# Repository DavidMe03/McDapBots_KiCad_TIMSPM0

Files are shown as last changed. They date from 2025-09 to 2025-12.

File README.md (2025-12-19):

# McDap Bots Pedagogical Robot

This project was created as a capstone project for the University of Virginia Department of Electrical and Computer Engineering. Our goal was to create a small robot which could be programmed by students, for use as a teaching aide in an embedded systems course. This repository contains the hardware files specific to the robot's main board.

**Authors**
- Colby Wise
- Pratik Pandit
- Austen Yun 
- David Merino
- Marc Rosenthal

**Advisors**: Todd DeLong and Adam Barnes 

**Features at a glance**
- 2 motors (PWM controlled), OLED screen (I2C), reflectance sensor (I2C), bump switches (GPIO), Bluetooth (UART), and infrared sensors (ADC)
- battery charging port and battery voltage display (press button to enable)
- support for TI and STM microcontrollers

## What is contained here

**Project Symbols/Footprints**

Symbols that are specific to this project such as the robot chassis. 

**Schematic File**

KiCad schematic file that shows the electrical connections of each component of the robot. 

**Layout File**

KiCad layout file that shows how the components are placed and routed on the PCB. 

**Bill of Materials Files**

BOM.xlsx contains a list of all the parts needed for the PCB.

Digikey_Parts_List.xlsx can be uploaded to Digikey to select the parts needed for one copy of this board.

## How to use this repository
1. Copy the repository locally to your computer
2. Using KiCad 8.0 (or higher version) open the file `MotorBoardv3_2.kicad_pro`
3. Generate necessary gerber files and order components
4. Follow the provided construction guide to build the robot

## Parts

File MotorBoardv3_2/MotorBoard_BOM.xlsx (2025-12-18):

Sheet: MotorBoardv3_2
Main PCB Parts
Id | Designator | Footprint | Quantity | Designation | Supplier | Link | Notes
1 | LED1 | APT1608CGCK | 1 | 3.3V | Digikey | APTD1608LSECK/J3-PF Kingbright | Optoelectronics | DigiKey (https://www.digikey.com/en/products/detail/kingbright/aptd1608lseck-j3-pf/5177446) | Red LED to indicate robot on/off
2 | CHARGE | APT1608CGCK | 1 | 3.3V | Digikey | APTD1608LZGCK Kingbright | Optoelectronics | DigiKey (https://www.digikey.com/en/products/detail/kingbright/APTD1608LZGCK/5177450) | Green LED to indicate battery charging
3 | R1,R2,R4,R13,R14 | R_0603_1608Metric | 5 | 4.7k | Digikey | RC0603FR-104K7L YAGEO | Resistors | DigiKey (https://www.digikey.com/en/products/detail/yageo/RC0603FR-104K7L/13694213) | Resistors
4 | R3,R12 | R_0603_1608Metric | 2 | 1.5k | Digikey | RC0603FR-071K5L YAGEO | Resistors | DigiKey (https://www.digikey.com/en/products/detail/yageo/RC0603FR-071K5L/726864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) | Resistors
5 | R5,R6 | R_1206_3216Metric | 2 | 0.1 | Digikey | RCWL1206R100JMEA Vishay Dale | Resistors | DigiKey (https://www.digikey.com/en/products/detail/vishay-dale/rcwl1206r100jmea/5777316) | Resistors
6 | R7 | R_0603_1608Metric | 1 | 750 | Digikey | RC0603JR-07750RL YAGEO | Resistors | DigiKey (https://www.digikey.com/en/products/detail/yageo/rc0603jr-07750rl/726825) | Resistor
7 | R8 | R_0603_1608Metric | 1 | 1.4k | Digikey | RC0603FR-071K4L YAGEO | Resistors | DigiKey (https://www.digikey.com/en/products/detail/yageo/RC0603FR-071K4L/726861) | Resistor
8 | R9 | R_0603_1608Metric | 1 | 68K | Digikey | RT0603FRE0768KL YAGEO | Resistors | DigiKey (https://www.digikey.com/en/products/detail/yageo/rt0603fre0768kl/1075464) | Resistor
9 | R10 | R_0603_1608Metric | 1 | 22K | Digikey | RC0603JR-0722KL YAGEO | Resistors | DigiKey (https://www.digikey.com/en/products/detail/yageo/rc0603jr-0722kl/726744) | Resistor
10 | R11 | R_0603_1608Metric | 1 | 150 | Digikey | RMCF0603FT150R Stackpole Electronics Inc | Resistors | DigiKey (https://www.digikey.com/en/products/detail/stackpole-electronics-inc/RMCF0603FT150R/1761314) | Resistor
11 | R_Sense1 | R_0603_1608Metric | 1 | 590m | Digikey | RLT0816-3-R590-FNH Delta Electronics/Cyntec | Resistors | DigiKey (https://www.digikey.com/en/products/detail/delta-electronics-cyntec/rlt0816-3-r590-fnh/9762157) | Resistor
12 | C1,C2,C3,C4,C5,C6,C7,C8 | CAPPM3528X210N | 8 | 10uF | Digikey | TAJB106K020RNJ KYOCERA AVX | Capacitors | DigiKey (https://www.digikey.com/en/products/detail/kyocera-avx/TAJB106K020RNJ/563780) | Capacitors (Polar)
13 | C9 | C_0603_1608Metric | 1 | 0.1uF | Digikey | CC0603KRX7R7BB104 YAGEO | Capacitors | DigiKey (https://www.digikey.com/en/products/detail/yageo/CC0603KRX7R7BB104/302822) | Capacitor
14 | C11,C15 | C_0603_1608Metric | 2 | 10uF | Digikey | TCM0J106M8R KYOCERA AVX | Capacitors | DigiKey (https://www.digikey.com/en/products/detail/kyocera-avx/TCM0J106M8R/1209640) | Capacitors (Polar)
15 | C12 | C_0603_1608Metric | 1 | 1uF | Digikey | CL10B105KP8NNNC Samsung Electro-Mechanics | Capacitors | DigiKey (https://www.digikey.com/en/products/detail/samsung-electro-mechanics/CL10B105KP8NNNC/3887604) | Capacitor
16 | C13,C14 | C_0603_1608Metric | 2 | 0.01uF | Digikey | C0603C103K5RACTU KEMET | Capacitors | DigiKey (https://www.digikey.com/en/products/detail/kemet/C0603C103K5RACTU/411090) | Capacitors
17 | D1 | D_DO-41_SOD81_P10.16mm_Horizontal | 1 | 1N4001 | Digikey | 1N4001-TP MCC (Micro Commercial Components) | Discrete Semiconductor Products | DigiKey (https://www.digikey.com/en/products/detail/mcc-micro-commercial-components/1N4001-TP/773688) | Rectifier Diode
18 | Q1 | TO-220-3_Vertical | 1 | TIP42A | Digikey | TIP42A STMicroelectronics | Discrete Semiconductor Products | DigiKey (https://www.digikey.com/en/products/detail/stmicroelectronics/TIP42A/603577) | PNP Transistor
19 | U1 | SOP65P640X120-17N | 1 | DRV8847PWPR | Digikey | DRV8847PWR Texas Instruments | Integrated Circuits (ICs) | DigiKey (https://www.digikey.com/en/products/detail/texas-instruments/DRV8847PWR/9954205) | Motor Driver IC
20 | U2 | SOT230P700X180-4N | 1 | LM2937IMP-5.0_NOPB | Digikey | LM2937IMP-5.0/NOPB Texas Instruments | Integrated Circuits (ICs) | DigiKey (https://www.digikey.com/en/products/detail/texas-instruments/LM2937IMP-5-0-NOPB/270743) | 5V Linear Regulator IC
21 | U3 | SOT230P700X180-4N | 1 | LM2937IMP-3.3_NOPB | Digikey | LM2937IMP-3.3 Texas Instruments | Integrated Circuits (ICs) | DigiKey (https://www.digikey.com/en/products/detail/texas-instruments/LM2937IMP-3-3/3701483) | 3.3V Linear Regulator IC
22 | U4 | SSD1306 | 1 | SSD1306 | Amazon | Amazon.com: Hosyond 5 Pcs 0.96 Inch OLED I2C IIC Display Module 12864 128x64 Pixel SSD1306 Mini Self-Luminous OLED Screen Board Compatible with Arduino Raspberry Pi (White) : Electronics (https://www.amazon.com/Hosyond-Display-Self-Luminous-Compatible-Raspberry/dp/B09T6SJBV5) | OLED Display Board, can be soldered directly onto PCB
23 | U7 | SOIC-16_3.9x9.9mm_P1.27mm | 1 | MAX712CSE | Digikey | MAX712CSE+T Analog Devices Inc./Maxim Integrated | Integrated Circuits (ICs) | DigiKey (https://www.digikey.com/en/products/detail/analog-devices-inc-maxim-integrated/MAX712CSE-T/1521014) | Charge Controller IC
24 | DS1 | PRT-14313 | 1 | ~ | Digikey | 14313 SparkFun Electronics | Industrial Automation and Controls | DigiKey (https://www.digikey.com/en/products/detail/sparkfun-electronics/14313/7564745) | Voltmeter LED Display
25 | S1 | SW_TS02-66-50-BK-160-LCR-D | 1 | TS02-66-50-BK-160-LCR-D | Digikey | TS02-66-50-BK-160-LCR-D Same Sky (Formerly CUI Devices) | Switches | DigiKey (https://www.digikey.com/en/products/detail/same-sky-formerly-cui-devices/TS02-66-50-BK-160-LCR-D/15634352) | SPST Tactile Switch for voltmeter
26 | J6 | 500SSP1S2M2QEA | 1 | 500SSP1S2M2QEA | Digikey | 500SSP1S2M2QEA E-Switch | Switches | DigiKey (https://www.digikey.com/en/products/detail/e-switch/500ssp1s2m2qea/1803993) | Robot power on/off slide switch
27 | J9 | TENSILITY_54-00127 | 1 | 54-00127 | Digikey | 54-00127 Tensility International Corp | Connectors, Interconnects | DigiKey (https://www.digikey.com/en/products/detail/tensility-international-corp/54-00127/9685436) | DC barrel jack port
28 | J2_J4,J3_J1 | LaunchPad | 2 | LaunchPad | Digikey | M20-8761042P Harwin Inc. | Connectors, Interconnects | DigiKey (https://www.digikey.com/en/products/detail/harwin-inc/M20-8761042P/3919957) | 20 position headers for connecting to the TI Launchpad
29 | J11,J12,J13 | SHDR3W50P0X200_1X3_650X240X440P | 3 | GP2Y0A41SK0F | Digikey | M22-7130342 Harwin Inc. | Connectors, Interconnects | DigiKey (https://www.digikey.com/en/products/detail/harwin-inc/M22-7130342/2264331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) | Female header pins for the IR Sensors
30 | J1,J2,J3,J4 | D2F-01L30-D3_5pin | 4 | Bump1,Bump2,Bump3,Bump4 | Digikey | SS-5GL2 Omron Electronics Inc-EMC Div | Switches | DigiKey (https://www.digikey.com/en/products/detail/omron-electronics-inc-emc-div/SS-5GL2/137204) | Bump switches
31 | J5 | RSLK_Chassis | 2 | RSLK2 | Digikey | CES-106-01-G-S Samtec Inc. | Connectors, Interconnects | DigiKey (https://www.digikey.com/en/products/detail/samtec-inc/ces-106-01-g-s/2172853) | Female header pins for the motors
32 | J10,J21 | PinHeader_1x04_P2.54mm_Vertical | 2 | Reflector Support, Reflector I2C | Digikey | PPTC041LFBN-RC Sullins Connector Solutions | Connectors, Interconnects | DigiKey (https://www.digikey.com/en/products/detail/sullins-connector-solutions/PPTC041LFBN-RC/810144) | Female header pins for the reflectance sensor array
33 | J7,J8,J15,J16,J17,J18 | PinHeader_1x02_P2.54mm_Vertical | 6 | XDS_VCC TP10, LP3.3,7.2,LP5.0,ELA,ERA | Digikey | TSW-120-07-L-S Samtec Inc. | Connectors, Interconnects | DigiKey (https://www.digikey.com/en/products/detail/samtec-inc/tsw-120-07-l-s/1101407) | Male header pins for jumpers
34 | TP1,TP2,TP3,TP4 | Testpoint_1x02_P2.54mm | 4 | +5V,+7.2V,GND,+3.3V | Digikey | TSW-120-07-L-S Samtec Inc. | Connectors, Interconnects | DigiKey (https://www.digikey.com/en/products/detail/samtec-inc/tsw-120-07-l-s/1101407) | Male header pins for test points
Additional Parts
Id | Designator | Footprint | Quantity | Designation | Supplier | Link | Notes
1 |  |  | 3 | IR Sensors | Digikey | GP2Y0A21YK0F SHARP/Socle Technology | Sensors, Transducers | DigiKey (https://www.digikey.com/en/products/detail/sharp-socle-technology/GP2Y0A21YK0F/720159) | 10-80cm IR Sensors
2 |  |  | 1 | Romi Chassis Kit | Pololu | Pololu - Romi Chassis Kit - Black (https://www.pololu.com/product/3500) | Robot chassis, wheels, motors, battery contacts
3 |  |  | 1 | Romi Encoder Pair Kit | Pololu | Pololu - Romi Encoder Pair Kit, 12 CPR, 3.5-18V (https://www.pololu.com/product/3542) | Pair of motor encoders
4 |  |  | 1 | TI MSPM0 Launchpad | Texas Instruments | LP-MSPM0G3507 Evaluation board | TI.com (https://www.ti.com/tool/LP-MSPM0G3507) | MSPM0 Launchpad, development board for the TI microcontroller
5 |  |  | 6 | Shunts | Digikey | 382811-8 TE Connectivity AMP Connectors | Connectors, Interconnects | DigiKey (https://www.digikey.com/en/products/detail/te-connectivity-amp-connectors/382811-8/293121) | Shunts for the jumpers
6 |  |  | 1 | Launchpad Power Connector | Digikey | SSQ-102-01-G-S Samtec Inc. | Connectors, Interconnects | DigiKey (https://www.digikey.com/en/products/detail/samtec-inc/SSQ-102-01-G-S/1110617) | 2-pin female header soldered onto the MSPM0 Launchpad

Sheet: BOM
Reflectance Sensor Adapter Board Parts

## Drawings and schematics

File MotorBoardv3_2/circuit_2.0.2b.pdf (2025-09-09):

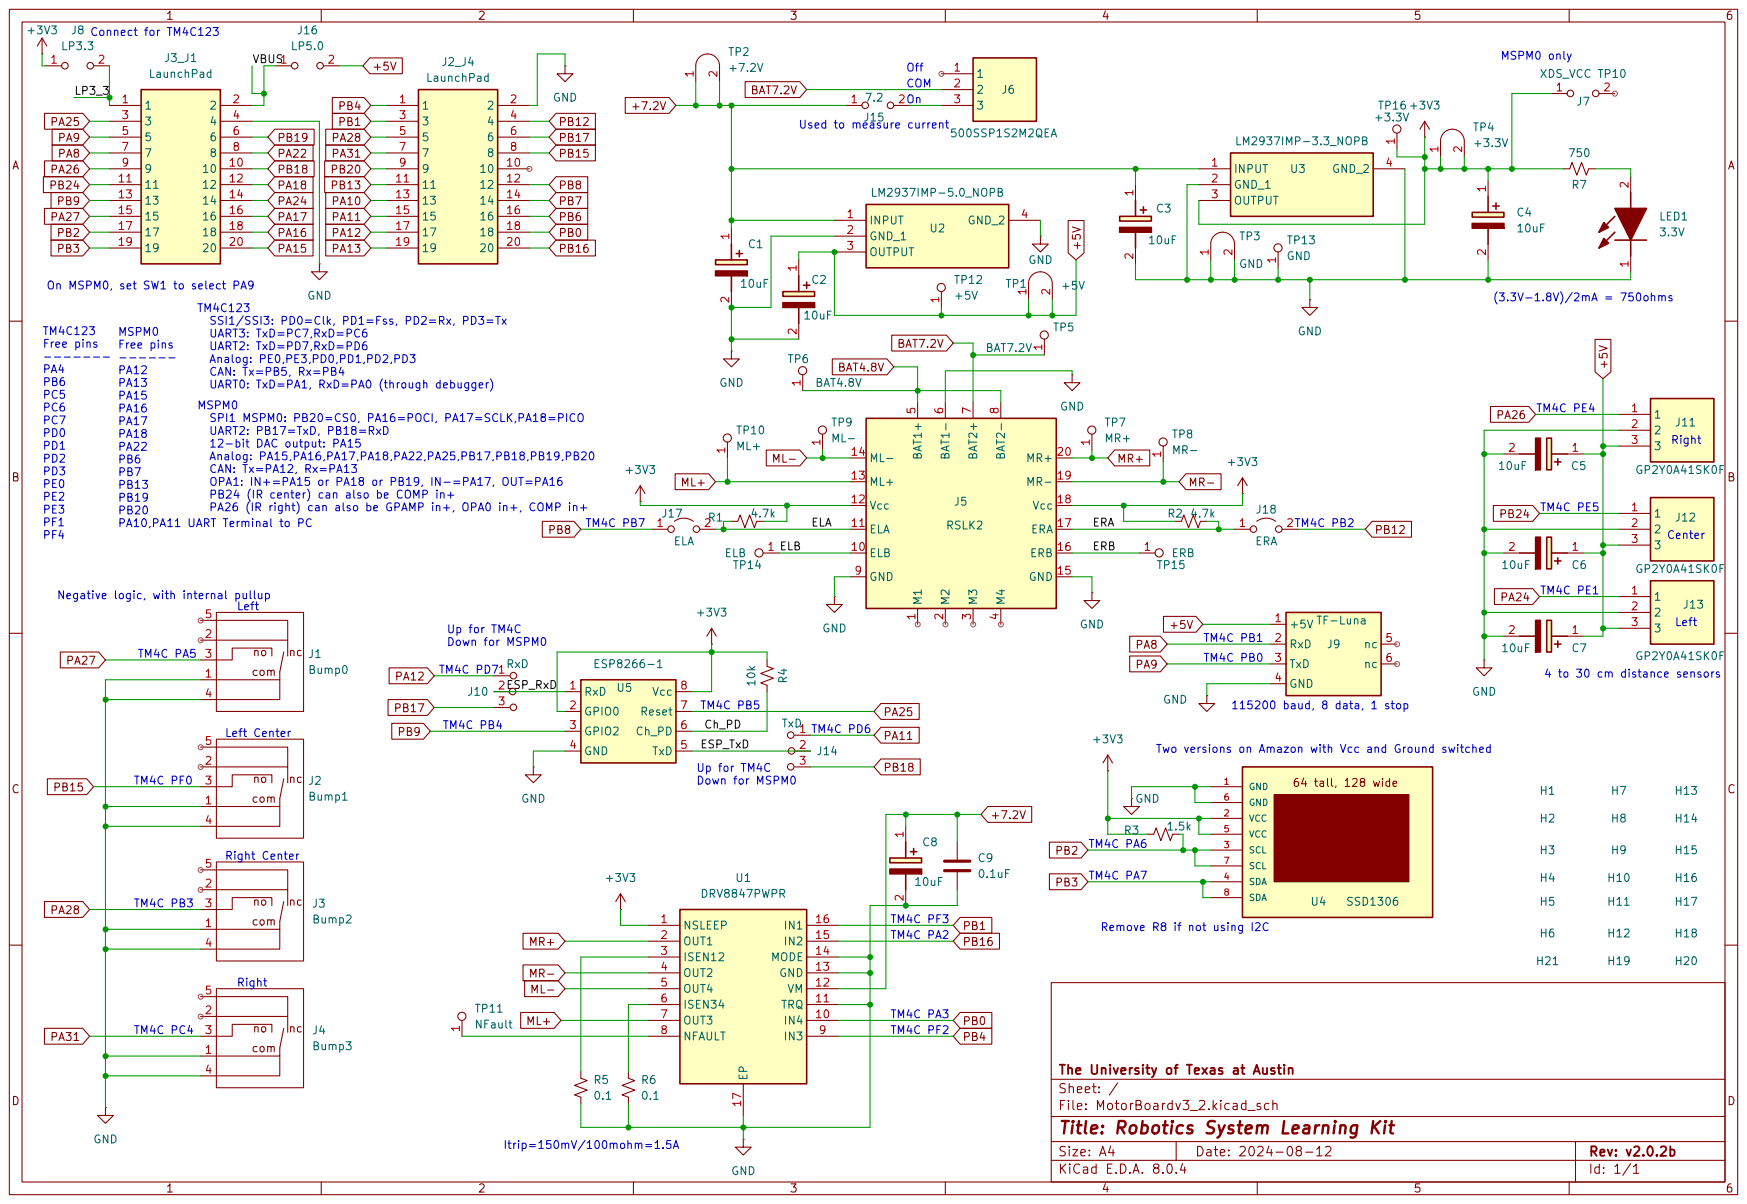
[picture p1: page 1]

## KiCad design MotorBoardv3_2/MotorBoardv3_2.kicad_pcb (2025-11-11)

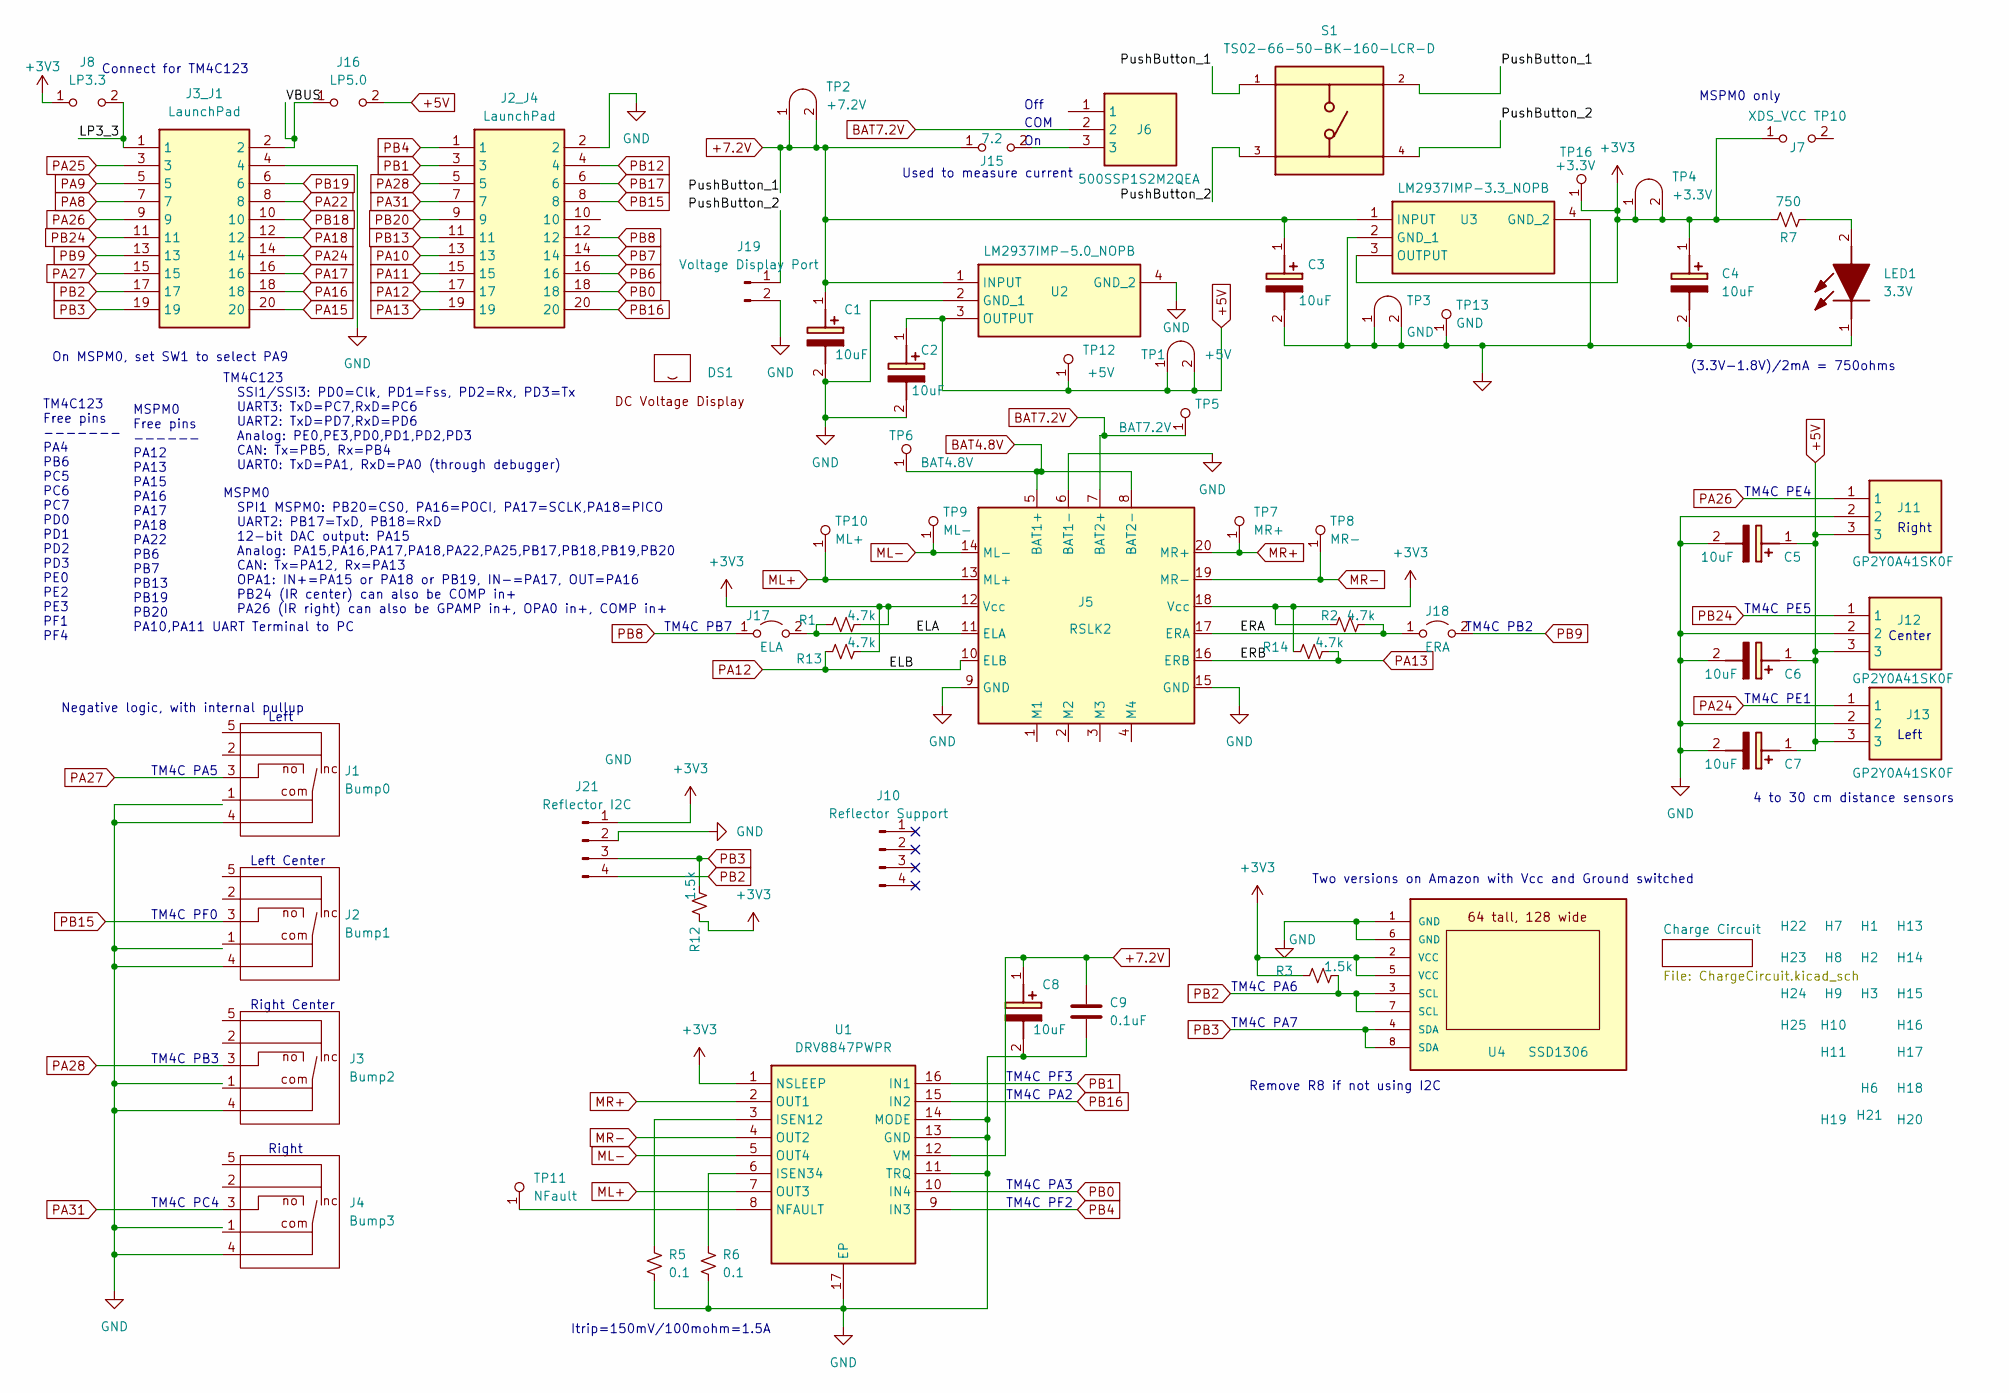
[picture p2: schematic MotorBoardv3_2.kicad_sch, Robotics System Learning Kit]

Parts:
C1, C2, C3, C4, C5, C6, C7, C8: 10uF; CAPPM3528X210N; Mouser Part Number 581-TAJB106K020R
C9: 0.1uF; C_0603_1608Metric; LCSC C5186689
DS1: PRT-14313
H1, H2, H3, H6, H7, H8, H9, H10, H11, H13, H14, H15, H16, H17, H18, H19, H20, H21, H22, H23, H24, H25: MountingHole_4_40
J1: Bump0; D2F-01L30-D3_5pin
J2: Bump1; D2F-01L30-D3_5pin
J2_J4, J3_J1: LaunchPad; Mouser Part Number 855-M20-8761042P
J3: Bump2; D2F-01L30-D3_5pin
J4: Bump3; D2F-01L30-D3_5pin
J5: RSLK2; RSLK_Chassis
J6: 500SSP1S2M2QEA; Mouser Part Number 612-500SSP1S2M2QEA
J7: XDS_VCC TP10; PinHeader_1x02_P2.54mm_Vertical; LCSC C5172712
J8: LP3.3; PinHeader_1x02_P2.54mm_Vertical; LCSC C5172712
J10: Reflector Support; PinHeader_1x04_P2.54mm_Vertical
J11, J12, J13: GP2Y0A41SK0F; SHDR3W50P0X200_1X3_650X240X440P; Mouser Part Number 855-M22-7130342
J15: 7.2; PinHeader_1x02_P2.54mm_Vertical; LCSC C5172712
J16: LP5.0; PinHeader_1x02_P2.54mm_Vertical; LCSC C5172712
J17: ELA; PinHeader_1x02_P2.54mm_Vertical
J18: ERA; PinHeader_1x02_P2.54mm_Vertical
J19: Voltage Display Port; SolderWire-0.15sqmm_1x02_P4mm_D0.5mm_OD1.5mm_Relief
J21: Reflector I2C; PinHeader_1x04_P2.54mm_Vertical
LED1: 3.3V; APT1608CGCK; Mouser Part Number 604-APTD1608LSECKJ3F
R1, R2, R13, R14: 4.7k; R_0603_1608Metric; LCSC C23162
R3, R12: 1.5k; R_0603_1608Metric; LCSC C216914
R5, R6: 0.1; R_1206_3216Metric; LCSC C2889036
R7: 750; R_0603_1608Metric; LCSC C365210
S1: TS02-66-50-BK-160-LCR-D; SW_TS02-66-50-BK-160-LCR-D; PARTREV 1.0
TP1: +5V; Testpoint_1x02_P2.54mm
TP2: +7.2V; Testpoint_1x02_P2.54mm
TP3: GND; Testpoint_1x02_P2.54mm
TP4: +3.3V; Testpoint_1x02_P2.54mm
TP5: BAT7.2V; Testpoint_1x1
TP6: BAT4.8V; Testpoint_1x1
TP7: MR+; Testpoint_1x1
TP8: MR-; Testpoint_1x1
TP9: ML-; Testpoint_1x1
TP10: ML+; Testpoint_1x1
TP11: NFault; Testpoint_1x1
TP12: +5V; Testpoint_1x1
TP13: GND; Testpoint_1x1
TP16: +3.3V; Testpoint_1x1
U1: DRV8847PWPR; SOP65P640X120-17N; Mouser Part Number 595-DRV8847PWPR
U2: LM2937IMP-5.0_NOPB; SOT230P700X180-4N; Mouser Part Number 926-LM2937IMP5.0NOPB
U3: LM2937IMP-3.3_NOPB; SOT230P700X180-4N; Mouser Part Number 926-LM2937IMP3.3NOPB
U4: SSD1306

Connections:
+3V3: C4.1 (+), J5.12 (Vcc), J5.18 (Vcc), J7.1 (A), J8.1 (A), J21.1, R1.2, R2.1, R3.1, R7.2, R12.1, R13.2, R14.1, TP4.1 (A), TP4.2 (B), TP16.1 (A), U1.1 (NSLEEP), U3.3 (OUTPUT), U4.2 (VCC), U4.5 (VCC)
+5V: C2.1 (+), C5.1 (+), C6.1 (+), C7.1 (+), J11.3, J12.3, J13.3, J16.2 (B), TP1.1 (A), TP1.2 (B), TP12.1 (A), U2.3 (OUTPUT)
+7.2V: C1.1 (+), C3.1 (+), C8.1 (+), C9.1, J15.1 (A), S1.1, S1.2, TP2.1 (A), TP2.2 (B), U1.12 (VM), U2.1 (INPUT), U3.1 (INPUT)
/ELA: J5.11 (ELA), J17.2 (B), R1.1
/ERA: J5.17 (ERA), J18.1 (A), R2.2
/LP3_3: J3_J1.1, J8.2 (B)
/PushButton_2: J19.1, S1.3, S1.4
/VBUS: J3_J1.2, J16.1 (A)
BAT4.8V: J5.5 (BAT1+), J5.8 (BAT2-), TP6.1 (A)
BAT7.2V: J5.7 (BAT2+), J6.2, TP5.1 (A); also elsewhere on the board
GND: C1.2 (-), C2.2 (-), C3.2 (-), C4.2 (-), C5.2 (-), C6.2 (-), C7.2 (-), C8.2 (-), C9.2, J1.4 (com), J2.4 (com), J2_J4.2, J3.4 (com), J3_J1.4, J4.4 (com), J5.6 (BAT1-), J5.9 (GND), J5.15 (GND), J11.2, J12.2, J13.2, J19.2, J21.2, LED1.1 (K), R5.2, R6.2, TP3.1 (A), TP3.2 (B), TP13.1 (A), U1.11 (TRQ), U1.13 (GND), U1.14 (MODE), U1.17 (EP), U2.2 (GND_1), U2.4 (GND_2), U3.2 (GND_1), U3.4 (GND_2), U4.1 (GND), U4.6 (GND); also elsewhere on the board
ML+: J5.13 (ML+), TP10.1 (A), U1.7 (OUT3)
ML-: J5.14 (ML-), TP9.1 (A), U1.5 (OUT4)
MR+: J5.20 (MR+), TP7.1 (A), U1.2 (OUT1)
MR-: J5.19 (MR-), TP8.1 (A), U1.4 (OUT2)
unnamed: J6.3, J15.2 (B)
unnamed: LED1.2 (A), R7.1
unnamed: TP11.1 (A), U1.8 (NFAULT)
unnamed: R5.1, U1.3 (ISEN12)
unnamed: R6.1, U1.6 (ISEN34)
PA8: J3_J1.7
PA9: J3_J1.5
PA10: J2_J4.13
PA11: J2_J4.15
PA12: J2_J4.17, J5.10 (ELB), R13.1
PA13: J2_J4.19, J5.16 (ERB), R14.2
PA15: J3_J1.20
PA16: J3_J1.18
PA17: J3_J1.16
PA18: J3_J1.12
PA22: J3_J1.8
PA24: J3_J1.14, J13.1
PA25: J3_J1.3
PA26: J3_J1.9, J11.1
PA27: J1.3 (no), J3_J1.15
PA28: J2_J4.5, J3.3 (no)
PA31: J2_J4.7, J4.3 (no)
PB0: J2_J4.18, U1.10 (IN4)
PB1: J2_J4.3, U1.16 (IN1)
PB2: J3_J1.17, J21.4, R3.2, U4.3 (SCL), U4.7 (SCL)
PB3: J3_J1.19, J21.3, R12.2, U4.4 (SDA), U4.8 (SDA)
PB4: J2_J4.1, U1.9 (IN3)
PB6: J2_J4.16
PB7: J2_J4.14
PB8: J2_J4.12, J17.1 (A)
PB9: J3_J1.13, J18.2 (B)
PB12: J2_J4.4
PB13: J2_J4.11
PB15: J2.3 (no), J2_J4.8
PB16: J2_J4.20, U1.15 (IN2)
PB17: J2_J4.6
PB18: J3_J1.10
PB19: J3_J1.6
PB20: J2_J4.9
PB24: J3_J1.11, J12.1

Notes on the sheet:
TM4C PB7
TM4C PE5
Negative logic, with internal pullup
TM4C PF2
TM4C PC4
Used to measure current
Right
TM4C PA3
MSPM0 Free pins ------ PA12 PA13 PA15 PA16 PA17 PA18 PA22 PB6 PB7 PB13 PB19 PB20 PA10,PA11 UART Terminal to PC
TM4C PB2
TM4C123 Free pins ------- PA4 PB6 PC5 PC6 PC7 PD0 PD1 PD2 PD3 PE0 PE2 PE3 PF1 PF4
Left Center
Connect for TM4C123
Left
TM4C PF3
TM4C PA6
MSPM0 SPI1 MSPM0: PB20=CS0, PA16=POCI, PA17=SCLK,PA18=PICO UART2: PB17=TxD, PB18=RxD 12-bit DAC output: PA15 Analog: PA15,PA16,PA17,PA18,PA22,PA25,PB17,PB18,PB19,PB20 CAN: Tx=PA12, Rx=PA13 OPA1: IN+=PA15 or PA18 or PB19, IN-=PA17, OUT=PA16 PB24 (IR center) can also be COMP in+ PA26 (IR right) can a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
TM4C PF0
Two versions on Amazon with Vcc and Ground switched
Itrip=150mV/100mohm=1.5A
TM4C PA5
Off
4 to 30 cm distance sensors
On MSPM0, set SW1 to select PA9
Remove R8 if not using I2C
Right Center
Center
TM4C PE4
(3.3V-1.8V)/2mA = 750ohms
TM4C PB3
TM4C PA7
MSPM0 only
COM
TM4C PE1
TM4C PA2
TM4C123 SSI1/SSI3: PD0=Clk, PD1=Fss, PD2=Rx, PD3=Tx UART3: TxD=PC7,RxD=PC6 UART2: TxD=PD7,RxD=PD6 Analog: PE0,PE3,PD0,PD1,PD2,PD3 CAN: Tx=PB5, Rx=PB4 UART0: TxD=PA1, RxD=PA0 (through debugger)

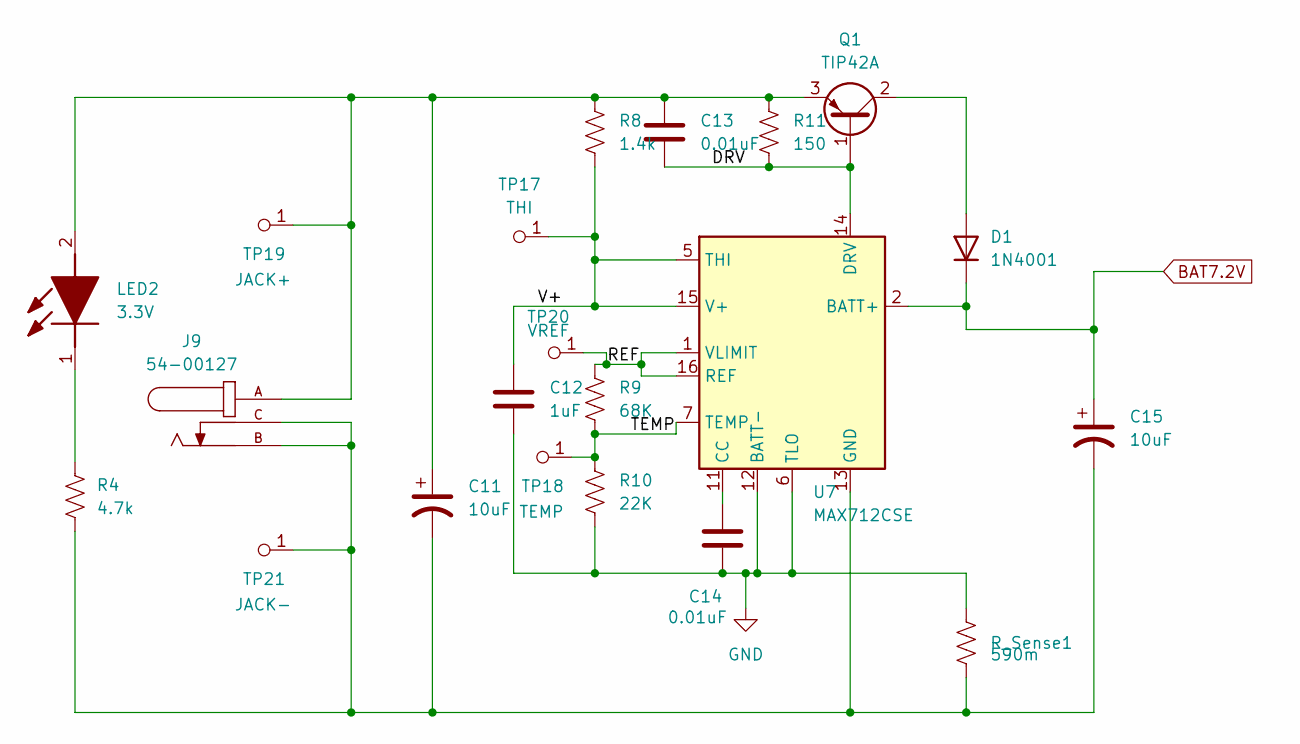
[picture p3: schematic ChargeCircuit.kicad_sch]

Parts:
C11, C15: 10uF; C_0603_1608Metric
C12: 1uF; C_0603_1608Metric
C13, C14: 0.01uF; C_0603_1608Metric
D1: 1N4001; D_DO-41_SOD81_P10.16mm_Horizontal
J9: 54-00127; TENSILITY_54-00127; PARTREV A
LED2: 3.3V; APT1608CGCK; Mouser Part Number 604-APTD1608LSECKJ3F
Q1: TIP42A; TO-220-3_Vertical
R4: 4.7k; R_0603_1608Metric
R8: 1.4k; R_0603_1608Metric
R9: 68K; R_0603_1608Metric
R10: 22K; R_0603_1608Metric
R11: 150; R_0603_1608Metric
R_Sense1: 590m; R_0603_1608Metric
TP17: THI; Testpoint_1x1
TP18: TEMP; Testpoint_1x1
TP19: JACK+; Testpoint_1x1
TP20: VREF; Testpoint_1x1
TP21: JACK-; Testpoint_1x1
U7: MAX712CSE; SOIC-16_3.9x9.9mm_P1.27mm

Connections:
/Charge Circuit/DRV: C13.2, Q1.1 (B), R11.2, U7.14 (DRV)
/Charge Circuit/REF: R9.1, TP20.1 (A), U7.1 (VLIMIT), U7.16 (REF)
/Charge Circuit/TEMP: R9.2, R10.1, TP18.1 (A), U7.7 (TEMP)
/Charge Circuit/V+: C12.1, R8.2, TP17.1 (A), U7.5 (THI), U7.15 (V+)
BAT7.2V: C15.1, D1.1 (K), U7.2 (BATT+); also elsewhere on the board
GND: C12.2, C14.2, R10.2, R_Sense1.1, U7.6 (TLO), U7.12 (BATT-); also elsewhere on the board
unnamed: D1.2 (A), Q1.2 (C)
unnamed 22: C11.1, C13.1, J9.A, LED2.2 (A), Q1.3 (E), R8.1, R11.1, TP19.1 (A); also elsewhere on the board
unnamed 23: LED2.1 (K), R4.1; also elsewhere on the board
unnamed: C11.2, C15.2, J9.B, J9.C, R4.2, R_Sense1.2, TP21.1 (A), U7.13 (GND)
unnamed: C14.1, U7.11 (CC)

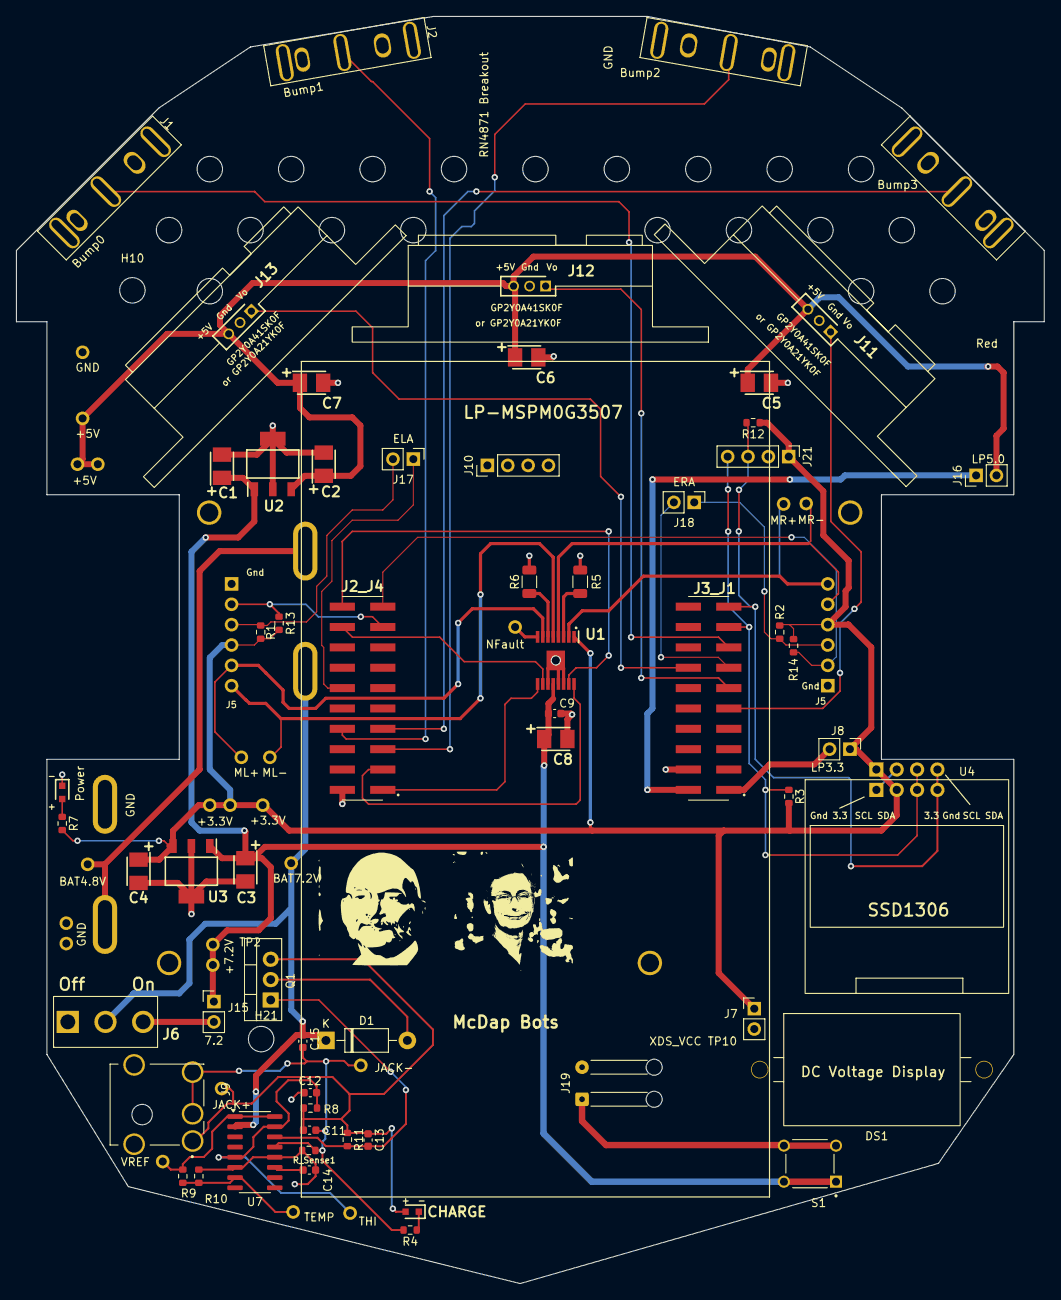
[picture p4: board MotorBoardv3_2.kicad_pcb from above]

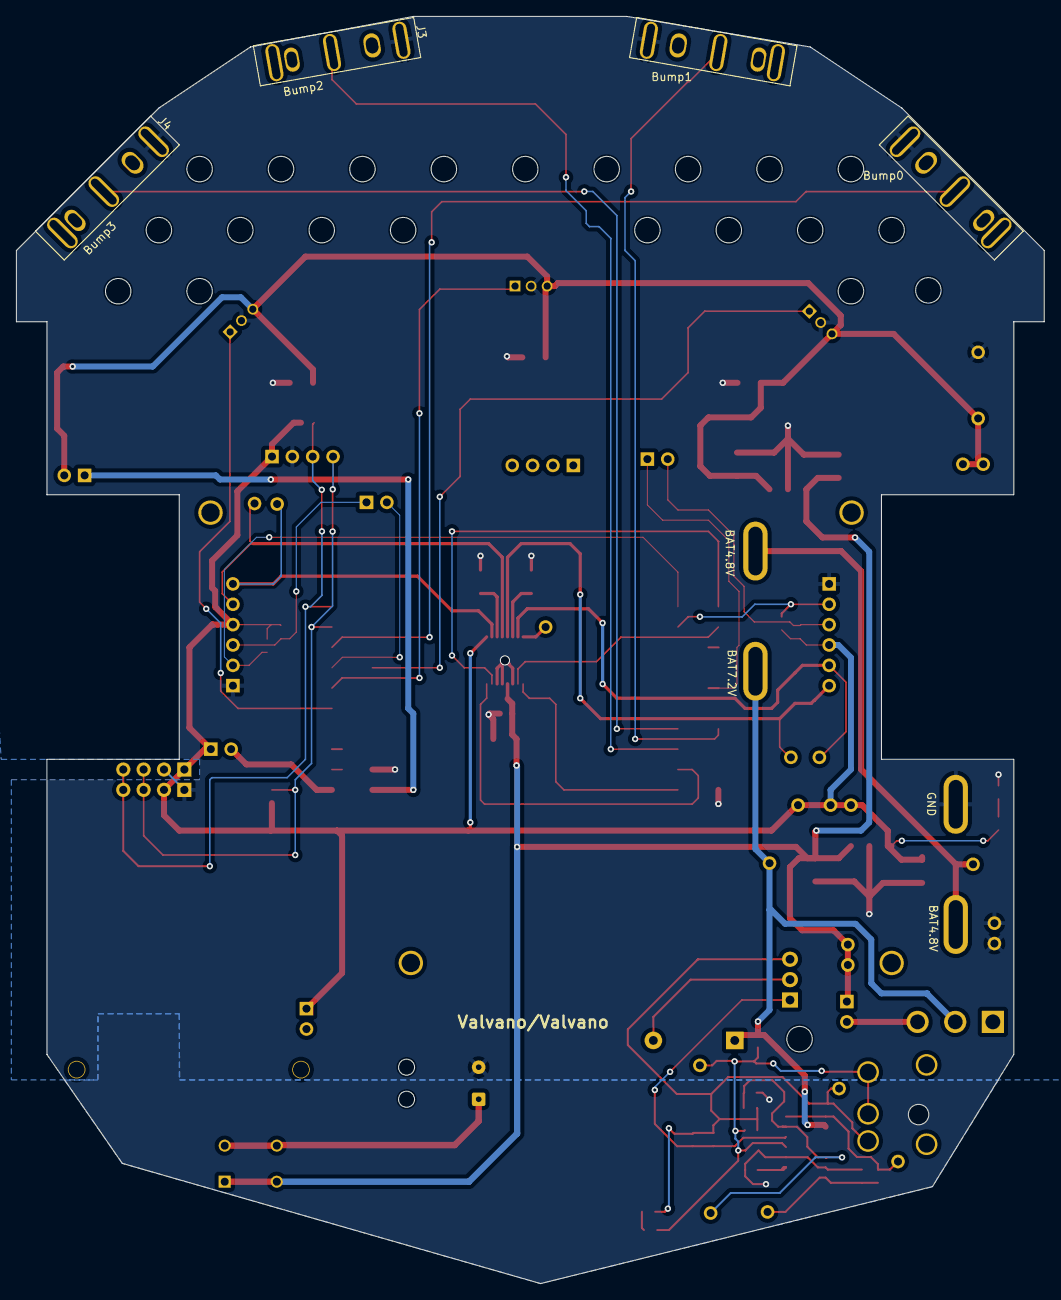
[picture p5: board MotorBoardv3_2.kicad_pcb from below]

Board: 2 copper layers, 128.3 x 158.1 mm, 102 parts (2 on the bottom side), 46 nets.

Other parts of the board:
CHARGE: 3.3V; APT1608CGCK

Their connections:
unnamed 22: CHARGE.2 (A); also elsewhere on the board
unnamed 23: CHARGE.1 (K); also elsewhere on the board

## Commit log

2025-09-19 Added voltage display
    Modified schematic and layout to include voltage display. Expanded board outline in layout to have more space at the back of the robot.
    [MotorBoardv3_2.kicad_pcb, MotorBoardv3_2.kicad_sch]
2025-09-23 Added charge controller schematic
    [McDapBots_Charge_Controller.kicad_sch]
2025-09-23 added bluetooth module to schematic
    [MotorBoardv3_2.kicad_sch, RN4871.kicad_sch]
2025-09-24 Completed Schematic w/ charge circuit, voltmeter, bluetooth, Reflective Sensor Port
    [ChargeCircuit.kicad_sch, MotorBoardv3_2.kicad_sch, RN4871.kicad_sch]
2025-09-28 corrected david's silly label
    [MotorBoardv3_2.kicad_sch]
2025-09-28 deleted esp8266 and tf-luna circuits from schematic
    [MotorBoardv3_2.kicad_sch]
2025-09-28 Deleted traces and text from ESP and Luna
    [MotorBoardv3_2.kicad_pcb]
2025-09-28 Fixed footprint not in library error
    [MotorBoardv3_2.kicad_pcb]
2025-09-28 Filled in ground plane where needed
    [MotorBoardv3_2.kicad_pcb]
2025-09-28 Created footprint for RN4871 through-hole
2025-09-29 Initial Charge Controller layout
    [ChargeCircuit.kicad_sch, MotorBoardv3_2.kicad_pcb]
2025-09-29 Label adjustements
    [ChargeCircuit.kicad_sch, MotorBoardv3_2.kicad_pcb]
2025-09-30 routed RN4871 eval board pins
    Also changed the positions of some silkscreen labels
    [MotorBoardv3_2.kicad_pcb, MotorBoardv3_2.kicad_sch, RN4871.kicad_sch]
2025-09-30 Added voltage display
    [MotorBoardv3_2.kicad_pcb, MotorBoardv3_2.kicad_sch]
2025-09-30 Added I2C port for reflective sensors
    [MotorBoardv3_2.kicad_pcb]
2025-09-30 changed I2C port placement on schematic
    [ChargeCircuit.kicad_sch, MotorBoardv3_2.kicad_sch]
2025-10-01 Removed uncessary ground trace
    [MotorBoardv3_2.kicad_pcb]
2025-10-01 Fixed DRC errors
    [MotorBoardv3_2.kicad_pcb]
2025-10-01 Fixed some silkscreen labels
    [MotorBoardv3_2.kicad_pcb]
2025-10-01 Increased trace widths
    Increased trace widths of 3.3V and GND signals going to Bluetooth module
    [MotorBoardv3_2.kicad_pcb]
2025-10-01 Added test points to Charge Circuit
    [ChargeCircuit.kicad_sch, MotorBoardv3_2.kicad_pcb]
2025-10-02 Changed Barrel Jack Footprint to incorporate through-hole connections
    [ChargeCircuit.kicad_sch, MotorBoardv3_2.kicad_pcb]
2025-10-02 Updated Labeling so Silkscreen is not offboard; Added some necessary changes
    [MotorBoardv3_2.kicad_pcb]
2025-10-03 Generated Gerber Files
    [MotorBoardv3_2-B_Cu.gbl, MotorBoardv3_2-B_Mask.gbs, MotorBoardv3_2-B_Paste.gbp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]
2025-10-03 Removed bottom silkscreen from gerbers
    Regenerated gerbers to not include bottom silkscreen layer
    [MotorBoardv3_2-B_Cu.gbl, MotorBoardv3_2-B_Mask.gbs, MotorBoardv3_2-B_Paste.gbp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]
2025-11-06 Removed old bluetooth module from schematic and layout
    [ChargeCircuit.kicad_sch, MotorBoardv3_2.kicad_pcb, MotorBoardv3_2.kicad_sch]
2025-11-06 added voltmeter button to schematic
    [MotorBoardv3_2.kicad_sch]
2025-11-06 added a possible footprint for button
    [MotorBoardv3_2.kicad_pcb, MotorBoardv3_2.kicad_sch]
2025-11-06 added button for DC Display
    [ChargeCircuit.kicad_sch, MotorBoardv3_2.kicad_pcb, MotorBoardv3_2.kicad_sch]
2025-11-06 Moved the transistor to not be under the MSPM0G3507
    [MotorBoardv3_2.kicad_pcb]
2025-11-07 Added reflector sensor support pins to schematic and layout
    [MotorBoardv3_2.kicad_pcb, MotorBoardv3_2.kicad_sch]
2025-11-07 Changed pin usages for rev 2
    [ChargeCircuit.kicad_sch, MotorBoardv3_2.kicad_pcb, MotorBoardv3_2.kicad_sch]
2025-11-07 added pullup resistors to encoders
    [MotorBoardv3_2.kicad_pcb, MotorBoardv3_2.kicad_sch]
2025-11-08 Fixed right motor header location
    Still need to move some traces around
    [MotorBoardv3_2.kicad_pcb]
2025-11-09 Updated traces
    [MotorBoardv3_2.kicad_pcb]
2025-11-10 added charging indicator led
    [ChargeCircuit.kicad_sch]
2025-11-11 added charge LED to layout
    [ChargeCircuit.kicad_sch, MotorBoardv3_2.kicad_pcb, MotorBoardv3_2.kicad_sch]
2025-11-11 Generated Gerbers
    Also modified silkscreen to indicate polarity of diode
    [MotorBoardv3_2-B_Cu.gbl, MotorBoardv3_2-B_Mask.gbs, MotorBoardv3_2-B_Paste.gbp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]
2025-12-18 Added BOM files
    [MotorBoard_BOM.xlsx, MotorBoard_Digikey_Parts_List.xlsx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]
